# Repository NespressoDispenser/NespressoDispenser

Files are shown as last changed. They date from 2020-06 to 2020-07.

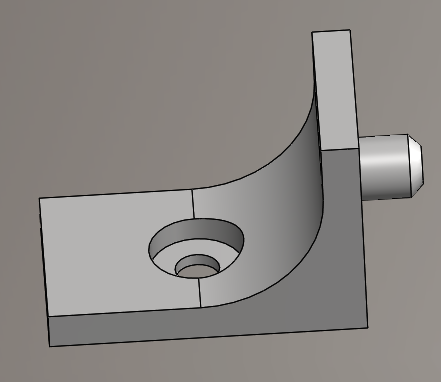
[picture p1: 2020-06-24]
3D prints/shelf bracket/shelf_bracket.png

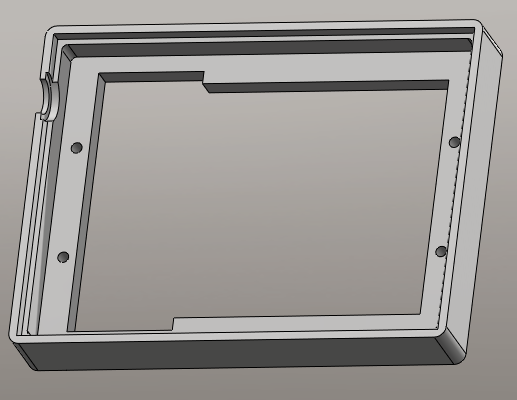
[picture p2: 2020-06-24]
3D prints/elatec reader mounting/reader_box_mounting.png

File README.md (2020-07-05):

# Nespresso dispenser machine
picture render
# Description
We are four students studying at the HEIG-VD in Switzerland and we've made this semester project. The purpose is to sell coffee capsule to anyone having a student card (Legic/Mifare) compatible with the Elatec reader.

- Affolter Luca: Modelling, system conception
- Fornerod Quentin: 3D printing, Github, RFID reader
- Fournier Loïc: Servomotors, LCD display
- Rosselli Jasmine: Touch sensors, Led strip

# Contact
If you have any question about the conception or any technichal interrogation, feel free to contact us:

Nespresso.Dispenser@gmail.com

# Youtube video
https://youtu.be/O0Zy7WqqgV4

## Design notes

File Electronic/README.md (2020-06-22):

# Description
The material we've used was mainly taken in the Fablab of the HEIG-VD

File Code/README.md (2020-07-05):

# Description
The Arduino codes are separated in two files:
- release version: contains the last code version uploaded on the machine

- test codes: contains primitives codes, some of them are not usefull but might be interesting

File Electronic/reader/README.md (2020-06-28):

# Description
Two softwares are available with the Elatec Reader:
- Director.exe
- AppBlaster.exe

# Director.exe
This programm is use to read any card via USB. In order to implement this, you have to load the right firmware USB

# AppBlaster.exe
This software allows you to custom the internal code of the Elatec reader. You have to create a source file (C programmed language) name it "App_HUS100_XXXXXXX_.c". You will then create a new firmware adding your source code file. Upload the firmware "TWN4_CCx322_HUS100_XXXXXXX.bix" in the device and you're ready to go. 

If something is unclear, please refer to the documentation "TWN4 API Reference DocRev24.pdf" and "TWN4 AppBlaster Config Cards User Guide DocRev10.pdf" and don't forget to check you wiring.

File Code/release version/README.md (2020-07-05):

# Description
We've used the *Arduino IDE* version 1.8.13 to compile and upload the code

The Arduino board is a ATMega 2560

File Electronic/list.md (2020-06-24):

# Description 
Complete list of material we bought for the project:
- 1x Elatec reader	T4DT-BB2BEL	
- 4x Inductive sensor	Lj6A3-2-z/BX	
- 2x Servo motors	SG92R	
- 2x Push button	(Any N-O button)	
- 2x40cm (2x26 leds) Led strip WS2812	
- 1x LCD screen 16x2	NHD-0216K1Z-NSW-FBW-L-ND 	
- 1x Arduino Mega	Clone	
- 1x SD module	Micro SD TF Card Adapter	
- 1x Sd card	(Any)	
- 1x Power supply	12VDC XXXXW	
- 4x Touch sensor	SH150917

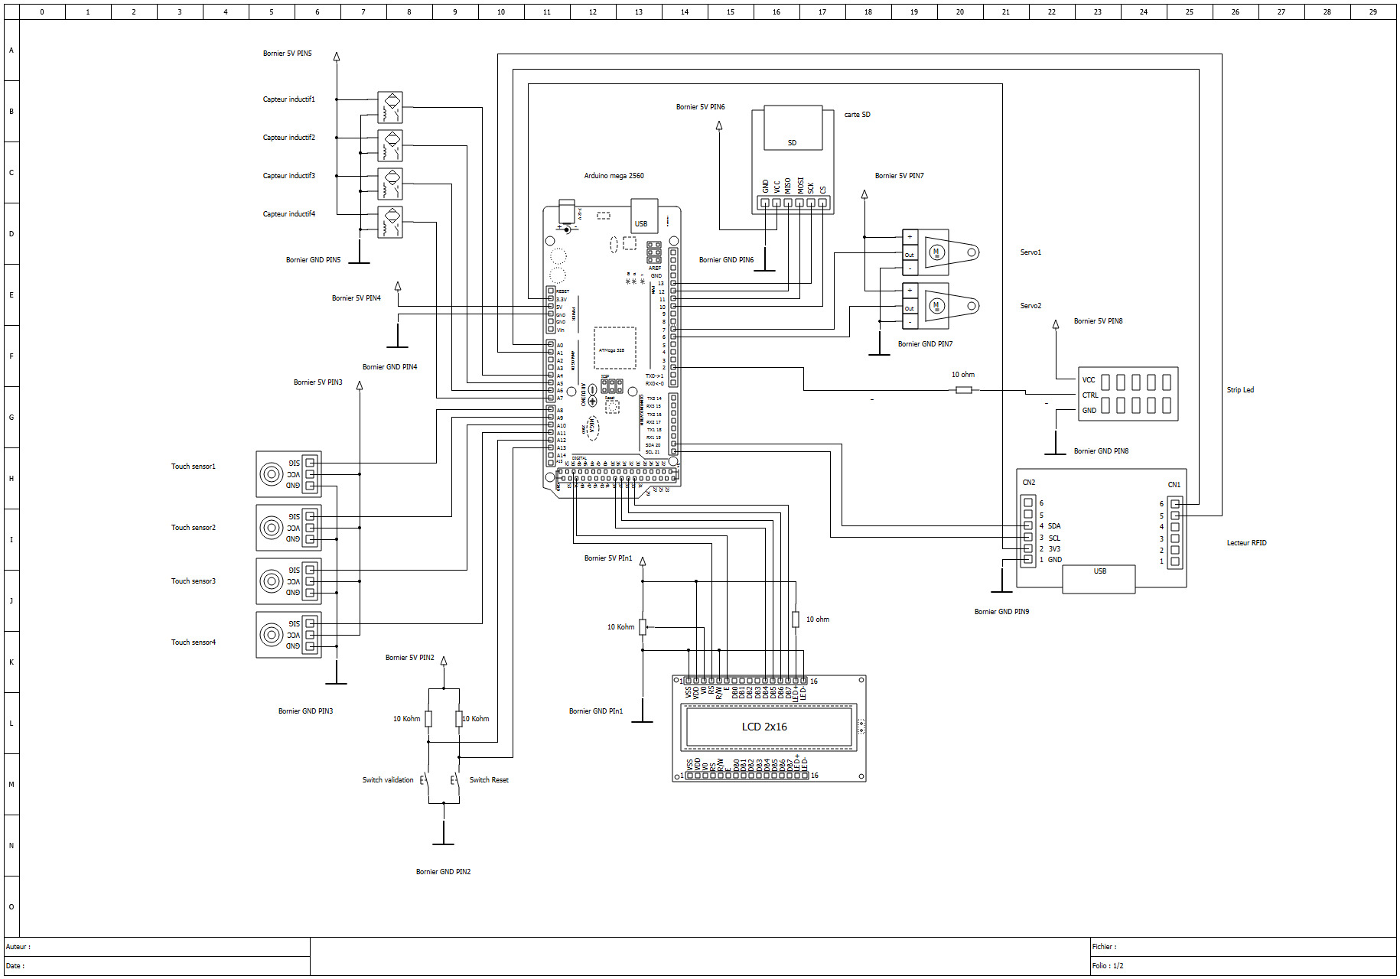
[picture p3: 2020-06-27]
Electronic/electronic_schematic.jpeg

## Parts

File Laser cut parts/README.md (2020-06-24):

# Description
The machine used for all the cuts (PPMA, MDF) is the Trotec Speedy 360. The thickness and the material of every part is mentionned in the file. Comments and filenames are in french.

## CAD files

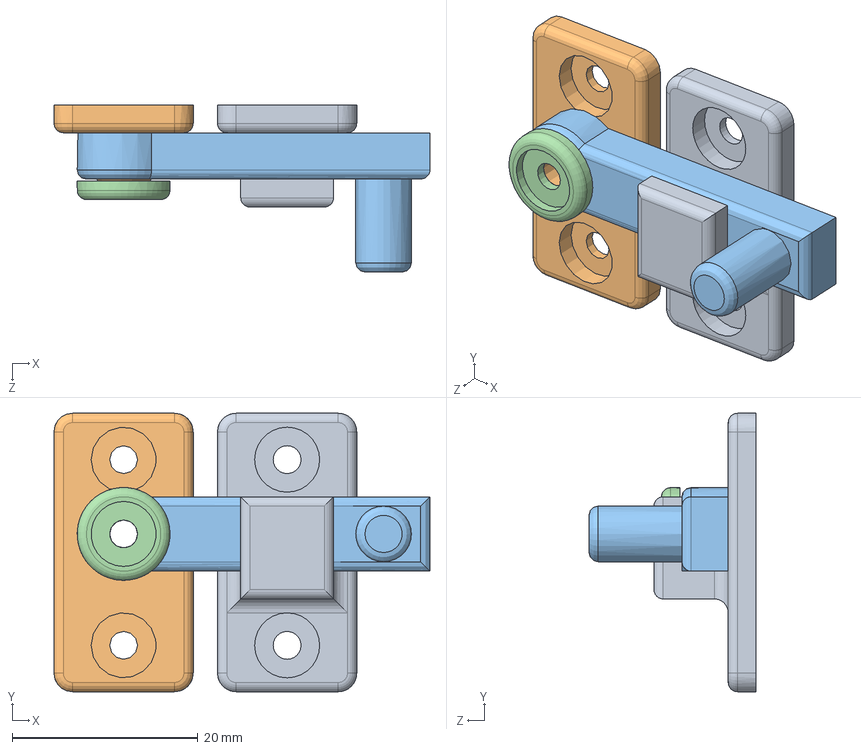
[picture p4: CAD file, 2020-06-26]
3D prints/door lock/asmb_door_lock.SLDASM
40.5 x 30.0 x 18.0 mm
door_lock_part1
door_lock_part2
door_lock_part3
door_lock_part4

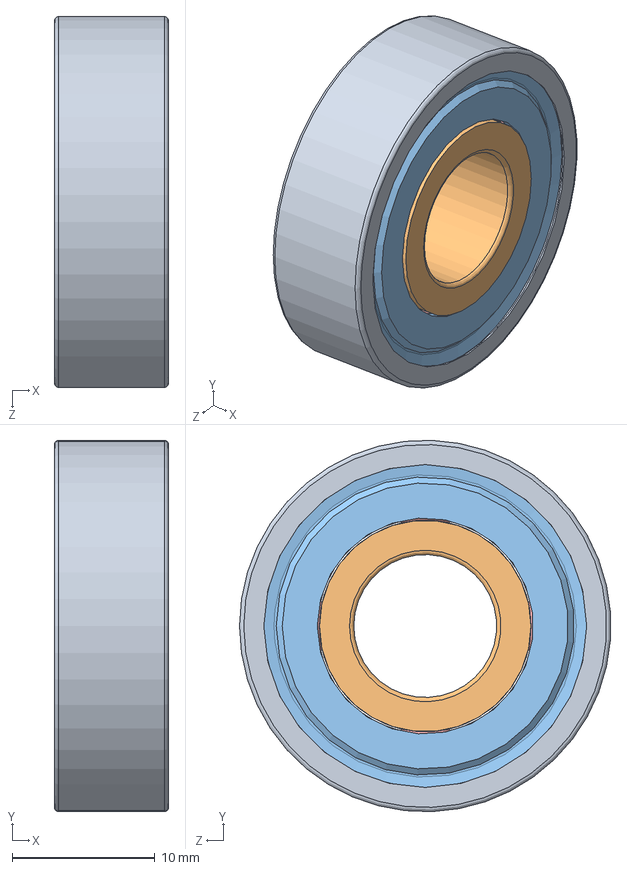
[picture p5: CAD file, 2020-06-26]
Assembly/roulement_6000-2z_1.SLDASM
8.00 x 26.0 x 26.0 mm
roulement_6000-2z_1_01
roulement_6000-2z_1_02
roulement_6000-2z_1_03
roulement_6000-2z_1_04
roulement_6000-2z_1_05

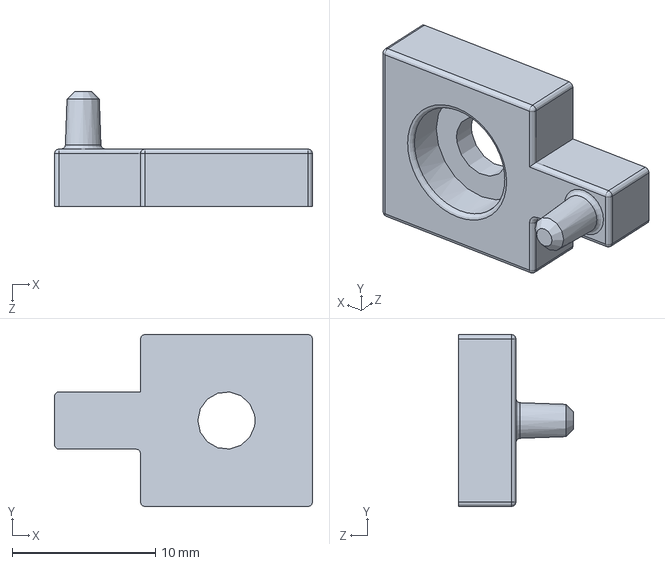
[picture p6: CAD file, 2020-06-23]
3D prints/arduino mega mounting/arduino_mega_mounting.SLDPRT
18.0 x 12.0 x 8.00 mm

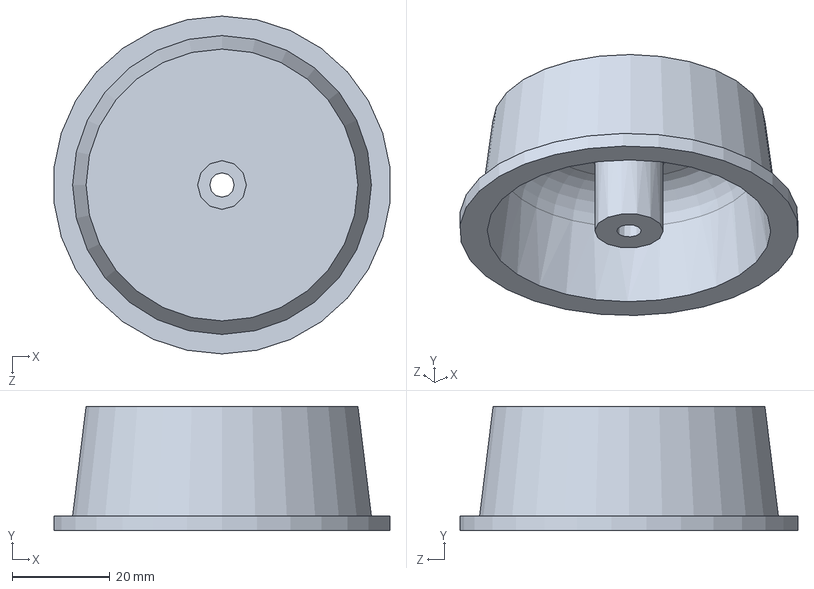
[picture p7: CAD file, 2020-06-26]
3D prints/cup holder/cup_holder_small_empty.SLDPRT
68.9 x 25.5 x 69.3 mm

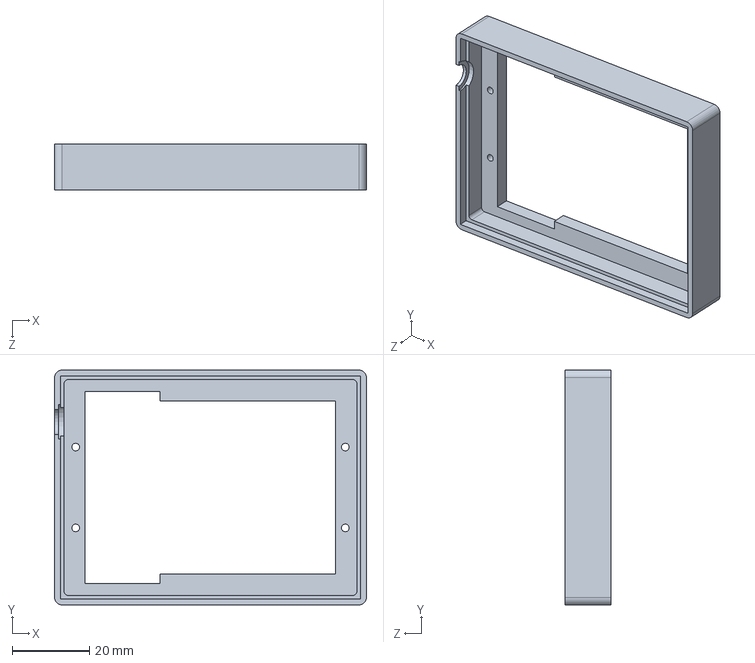
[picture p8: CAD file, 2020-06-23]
3D prints/elatec reader mounting/reader_box_mounting.SLDPRT
81.0 x 61.0 x 12.0 mm

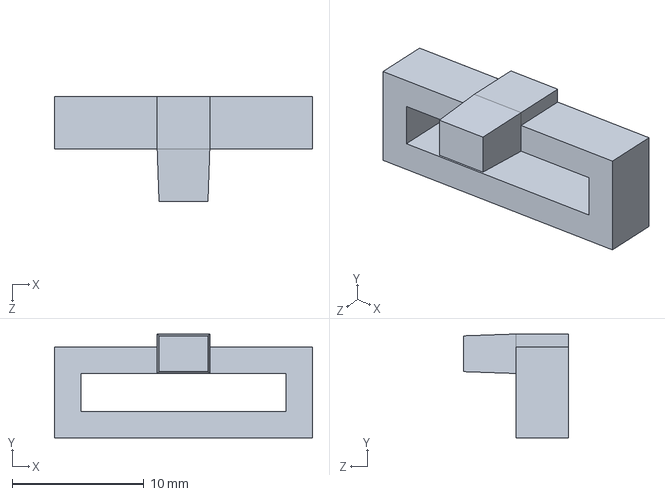
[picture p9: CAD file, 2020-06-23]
3D prints/encoding lug reader/encoding_lug_reader.SLDPRT
19.6 x 7.90 x 8.00 mm

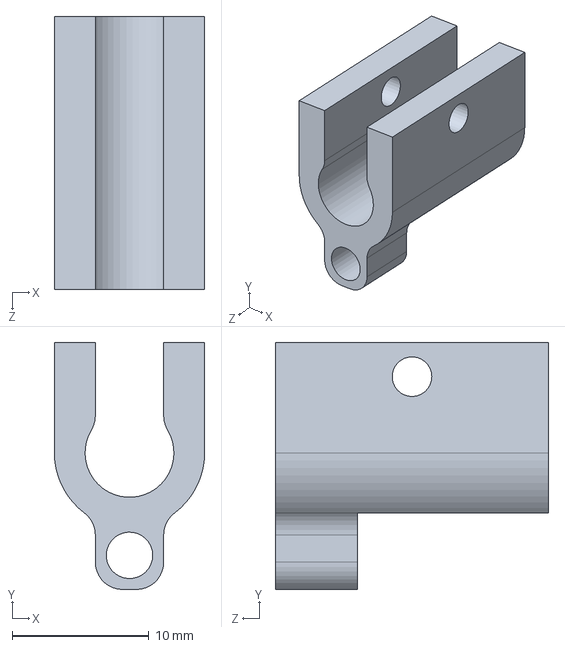
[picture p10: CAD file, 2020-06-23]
3D prints/inductive sensor mounting/inductive_sensor.SLDPRT
11.0 x 18.1 x 20.0 mm

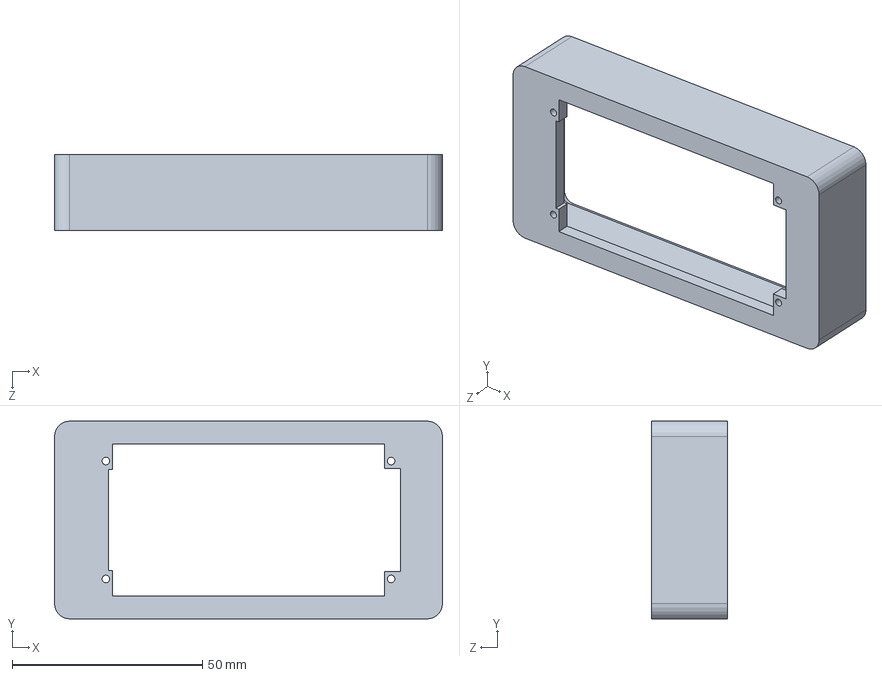
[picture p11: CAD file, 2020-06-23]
3D prints/LCD mounting/LCD_box_mounting.SLDPRT
102.0 x 52.0 x 20.0 mm

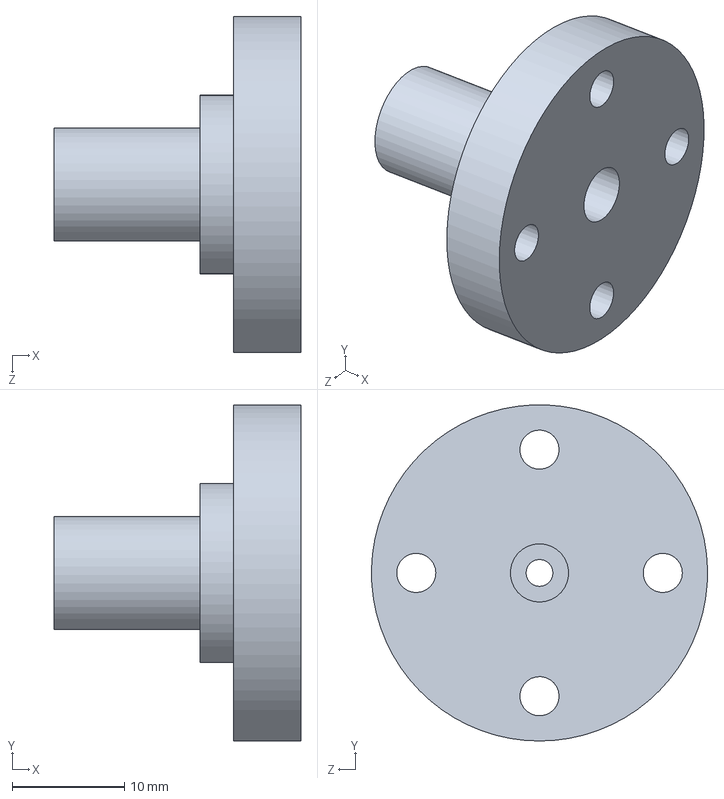
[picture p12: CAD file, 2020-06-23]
3D prints/motor coupling SG92/motor_coupling_sg92.SLDPRT
22.0 x 30.0 x 30.0 mm

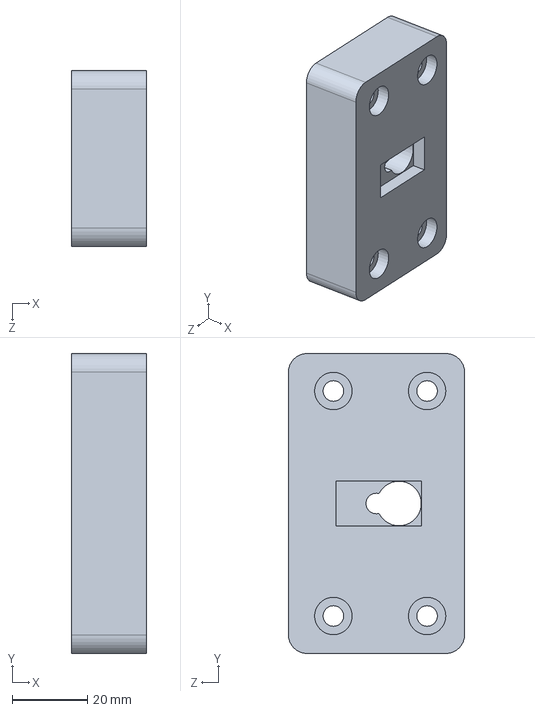
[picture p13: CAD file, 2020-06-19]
3D prints/motor mounting/motor_coupling.SLDPRT
20.0 x 80.0 x 47.0 mm

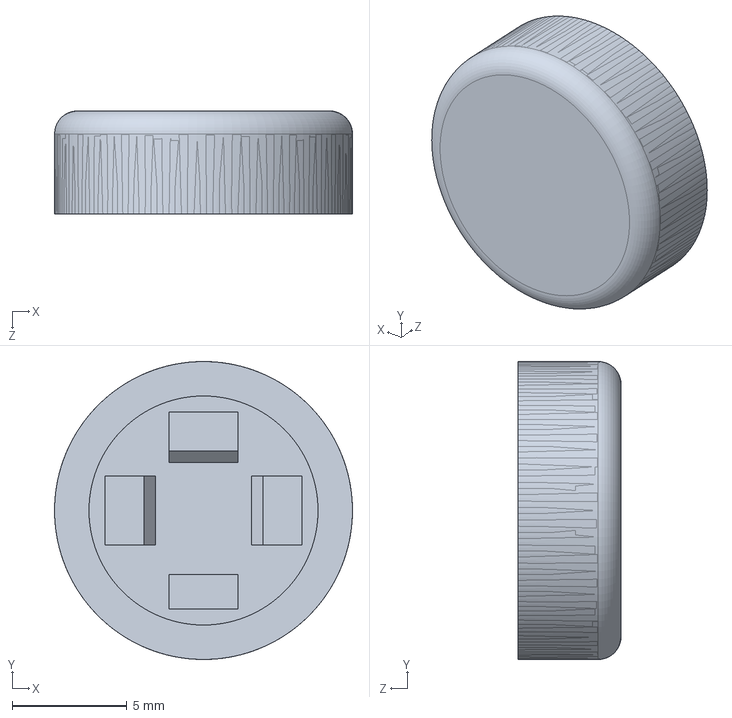
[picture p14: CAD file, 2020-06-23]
3D prints/push button cover/push_button_cover.SLDPRT
13.0 x 13.0 x 4.50 mm

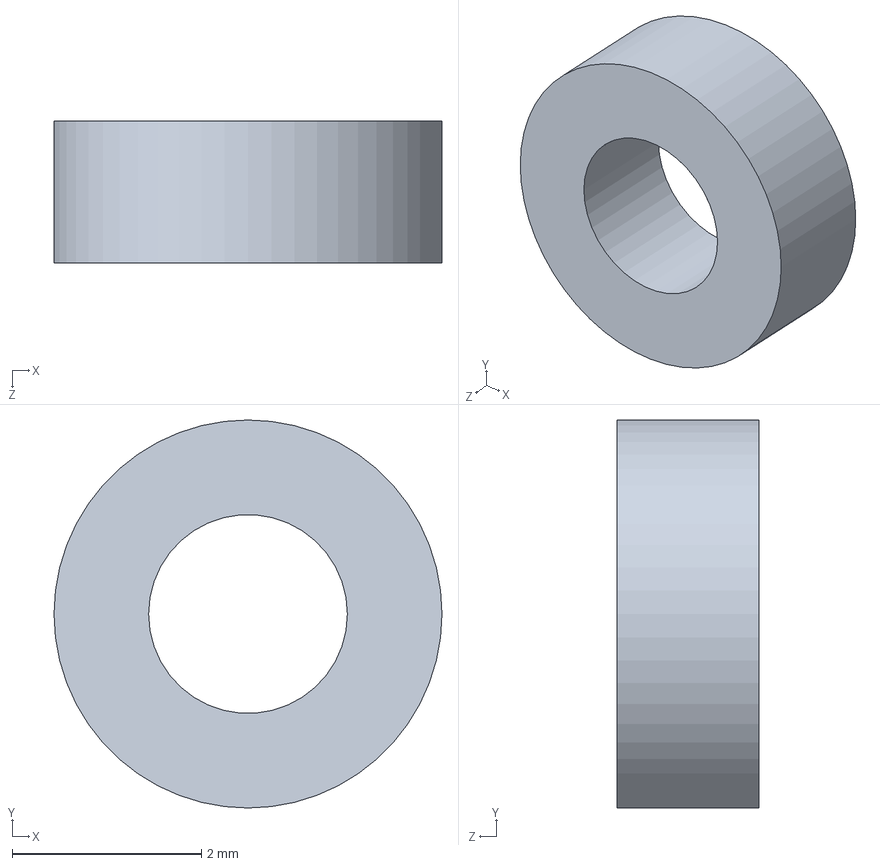
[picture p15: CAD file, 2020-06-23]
3D prints/SD module spacer/SD_module_spacer.SLDPRT
4.10 x 4.10 x 1.50 mm

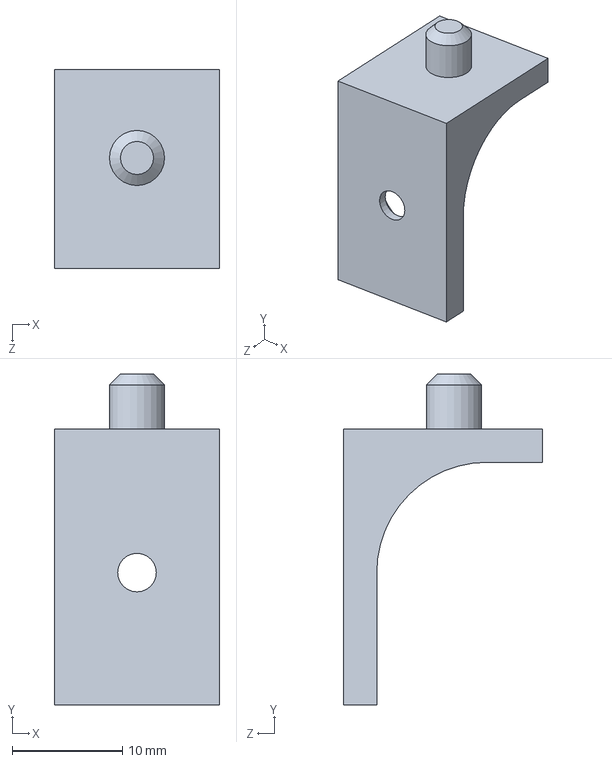
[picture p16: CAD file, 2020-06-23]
3D prints/shelf bracket/shelf bracket.SLDPRT
15.0 x 30.0 x 18.0 mm

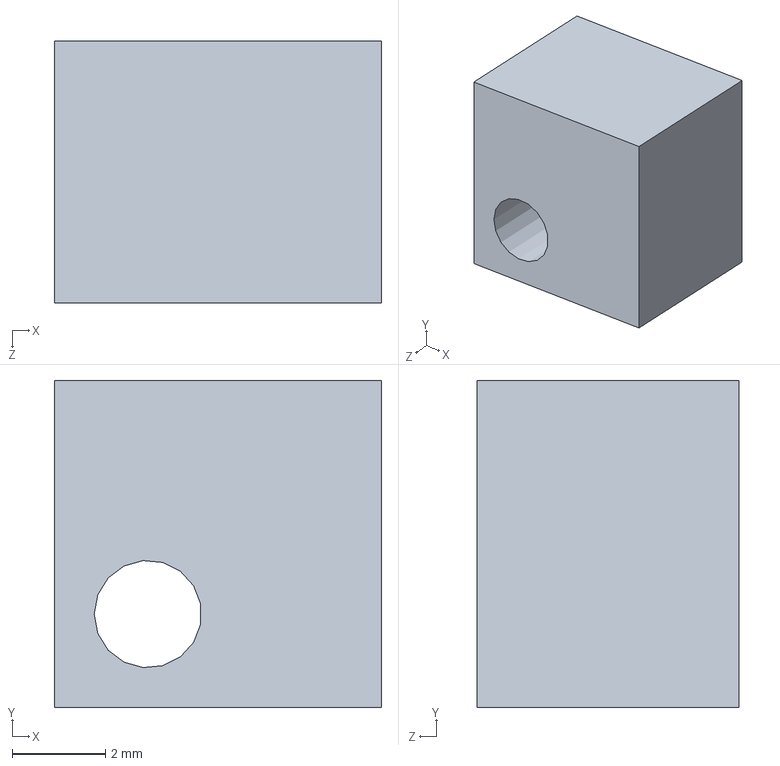
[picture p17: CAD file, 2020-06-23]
3D prints/touch sensor mounting/touch_sensor_mounting.SLDPRT
7.00 x 7.00 x 5.60 mm

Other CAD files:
Laser cut parts/plexiglass board (PMMA)/03_00 front pannel/03_00_Plexi_face.DXF
Laser cut parts/plexiglass board (PMMA)/03_01 merchandiser capsule pannel/03_01_Plexi_prsentoire.DXF
Laser cut parts/plexiglass board (PMMA)/03_02 led strip cover/03_02_Plexiglas_prsentoire_capsule.DXF
Laser cut parts/wooden board (MDF)/00_00 back pannel/00_00_Panneau_arriere.DXF
3D prints/LCD mounting/LCD_box_cover.SLDPRT
3D prints/LCD mounting/LCD_box_cover.STL
3D prints/LCD mounting/LCD_box_mounting.STL
3D prints/SD module spacer/SD_module_spacer.STL
3D prints/arduino mega mounting/arduino_mega_mounting.STL
3D prints/cup holder/cup_holder_big_empty.SLDPRT
3D prints/cup holder/cup_holder_big_empty.STL
3D prints/cup holder/cup_holder_small_empty.STL
3D prints/door lock/door_lock_part1.SLDPRT
3D prints/door lock/door_lock_part1.STL
3D prints/door lock/door_lock_part2.SLDPRT
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

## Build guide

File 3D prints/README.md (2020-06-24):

# Description
This folder contain all the files of the 3D printed parts. Each folder contains 3 files: 
- Stereolithographics files (.STL) 
- Modelised part (.SLDPRT)
- Picture (.png/.JPEG)

# Printing
The slicer software used is *Cura V4.6*, printing parameters will change upon the printing machine and won't be mentionned.
All impressions are made of PLA

# Modelling
All parts have been modelised with *Solidworks 2018 SP5.0* 

# Render
A picture of each modelised parts 

# Complementary informations
The file *list.md* specifies the number of each printed part used for the construction

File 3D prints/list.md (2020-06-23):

# Description
The list mentions the number of each piece printed for the project. The number of 3D prints may be different depending on your design choice.
# 3D parts
- 1x LCD mounting
- 4x SD module spacer
- 4x arduino mega mounting
- 1x door lock (each part)
- 1x elactec reader mounting (each part)
- 2x encoding lug reader
- 4x inductive sensor mounting
- 2x motor coupling SG92
- 2x motor mounting
- 2x push button cover (different colors)
- 4x shelf bracket
- 8x touch sensor mounting

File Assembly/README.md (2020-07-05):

# Render
modelling_machine

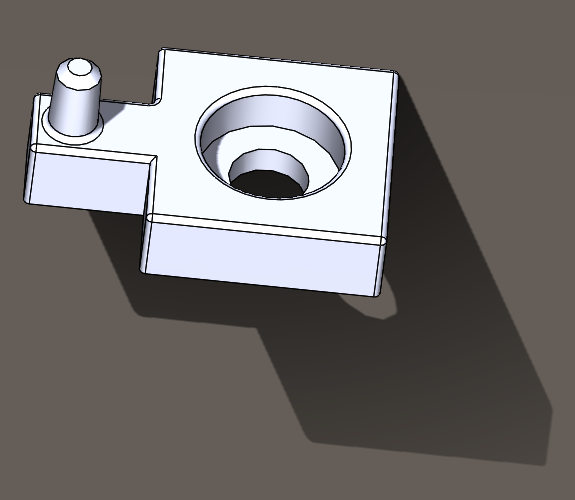
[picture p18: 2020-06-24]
3D prints/arduino mega mounting/arduino_mounting.png

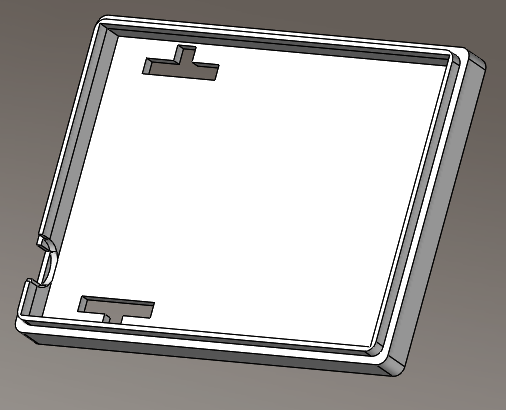
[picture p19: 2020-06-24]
3D prints/elatec reader mounting/reader_box_cover.png

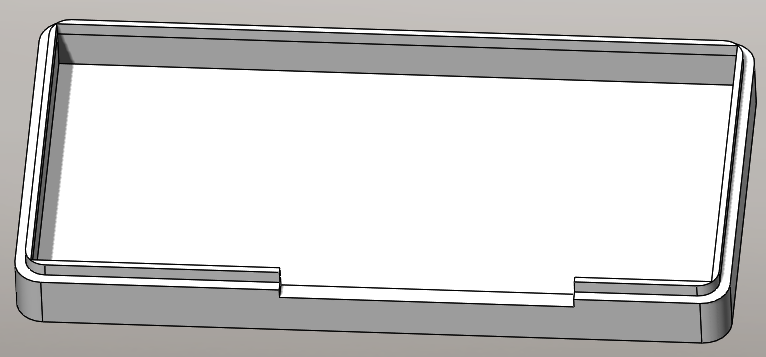
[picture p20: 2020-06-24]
3D prints/LCD mounting/LCD_box_cover.png

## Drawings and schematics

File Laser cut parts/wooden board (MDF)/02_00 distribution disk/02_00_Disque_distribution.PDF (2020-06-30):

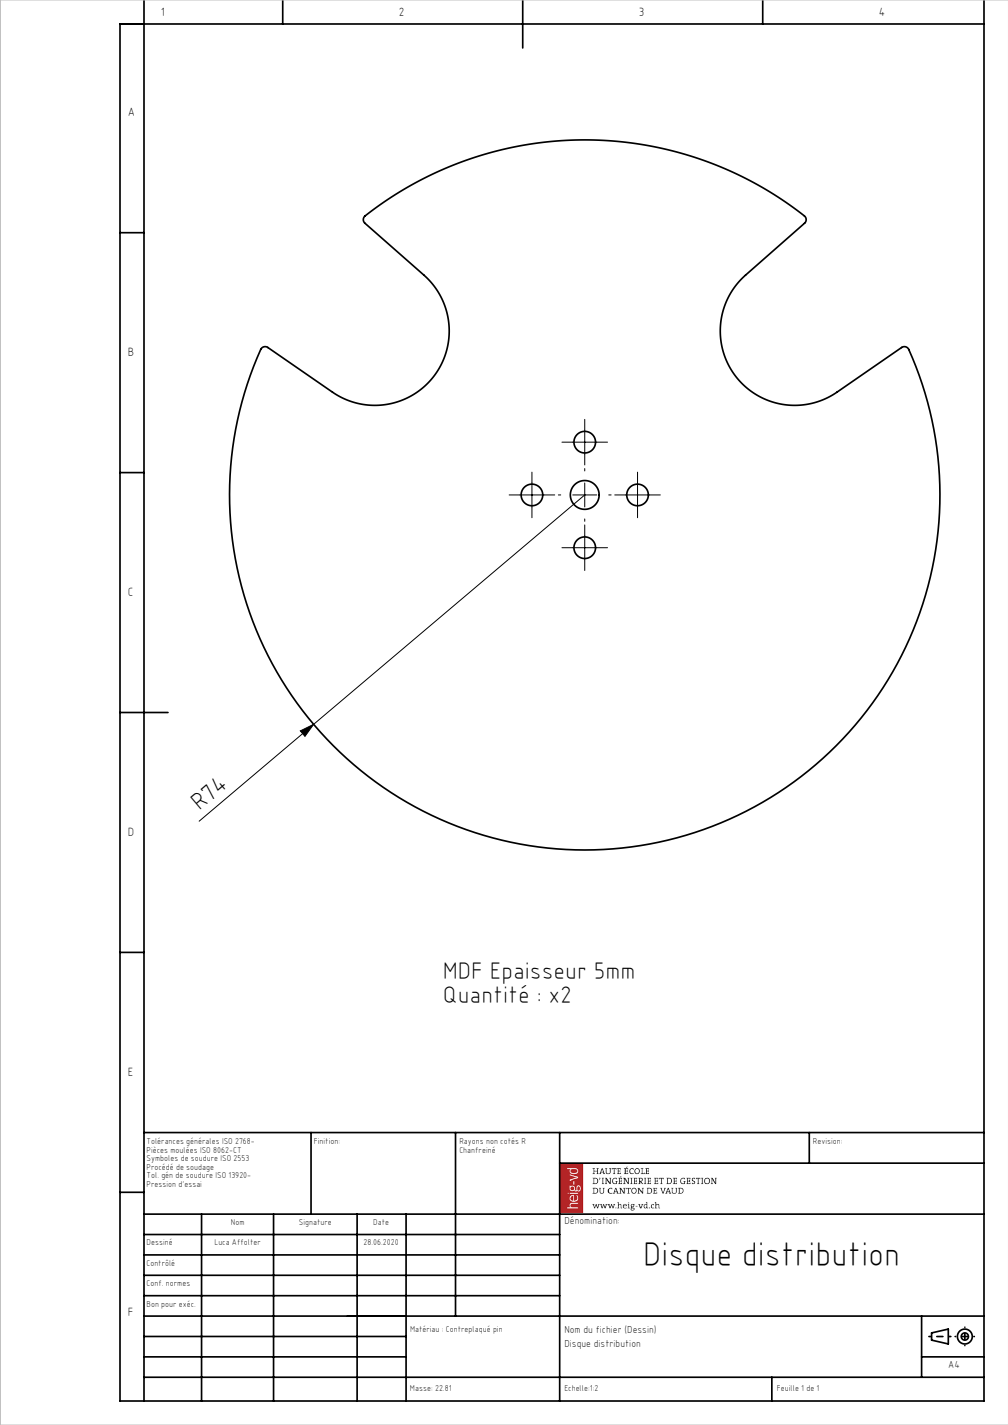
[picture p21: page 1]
MDF Epaisseur 5mm Quantité : x2; Masse: 22.81; Conf. normes; Bon pour exéc.; Feuille 1 de 1; Luca Affolter; Disque distribution

Tolérances générales ISO 2768-
Pièces moulées ISO 8062-CT
Symboles de soudure ISO 2553
Procédé de soudage
Tol. gén de soudure ISO 13920-
Pression d'essai

Rayons non cotés R
Chanfreiné

Matériau : Contreplaqué pin

Nom du fichier (Dessin)
Disque distribution

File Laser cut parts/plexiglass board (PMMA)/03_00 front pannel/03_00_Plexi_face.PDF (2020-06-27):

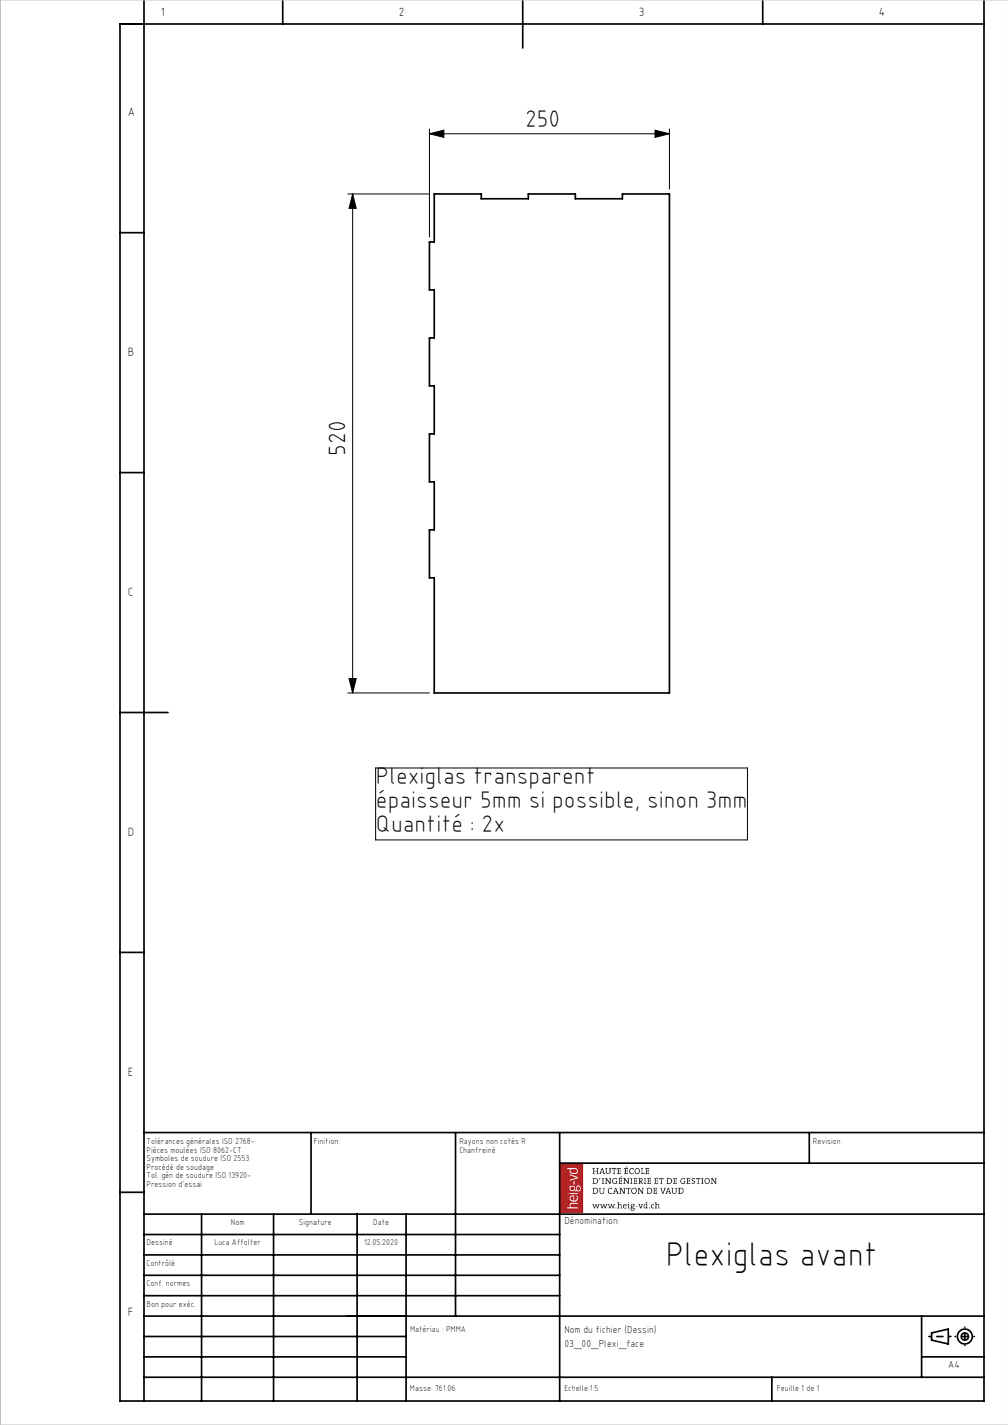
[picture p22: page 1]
Matériau : PMMA; Masse: 761.06; Conf. normes; Bon pour exéc.; Feuille 1 de 1; Luca Affolter; Plexiglas avant

Plexiglas transparent
épaisseur 5mm si possible, sinon 3mm
Quantité : 2x

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

Rayons non cotés R
Chanfreiné

Nom du fichier (Dessin)
03_00_Plexi_face

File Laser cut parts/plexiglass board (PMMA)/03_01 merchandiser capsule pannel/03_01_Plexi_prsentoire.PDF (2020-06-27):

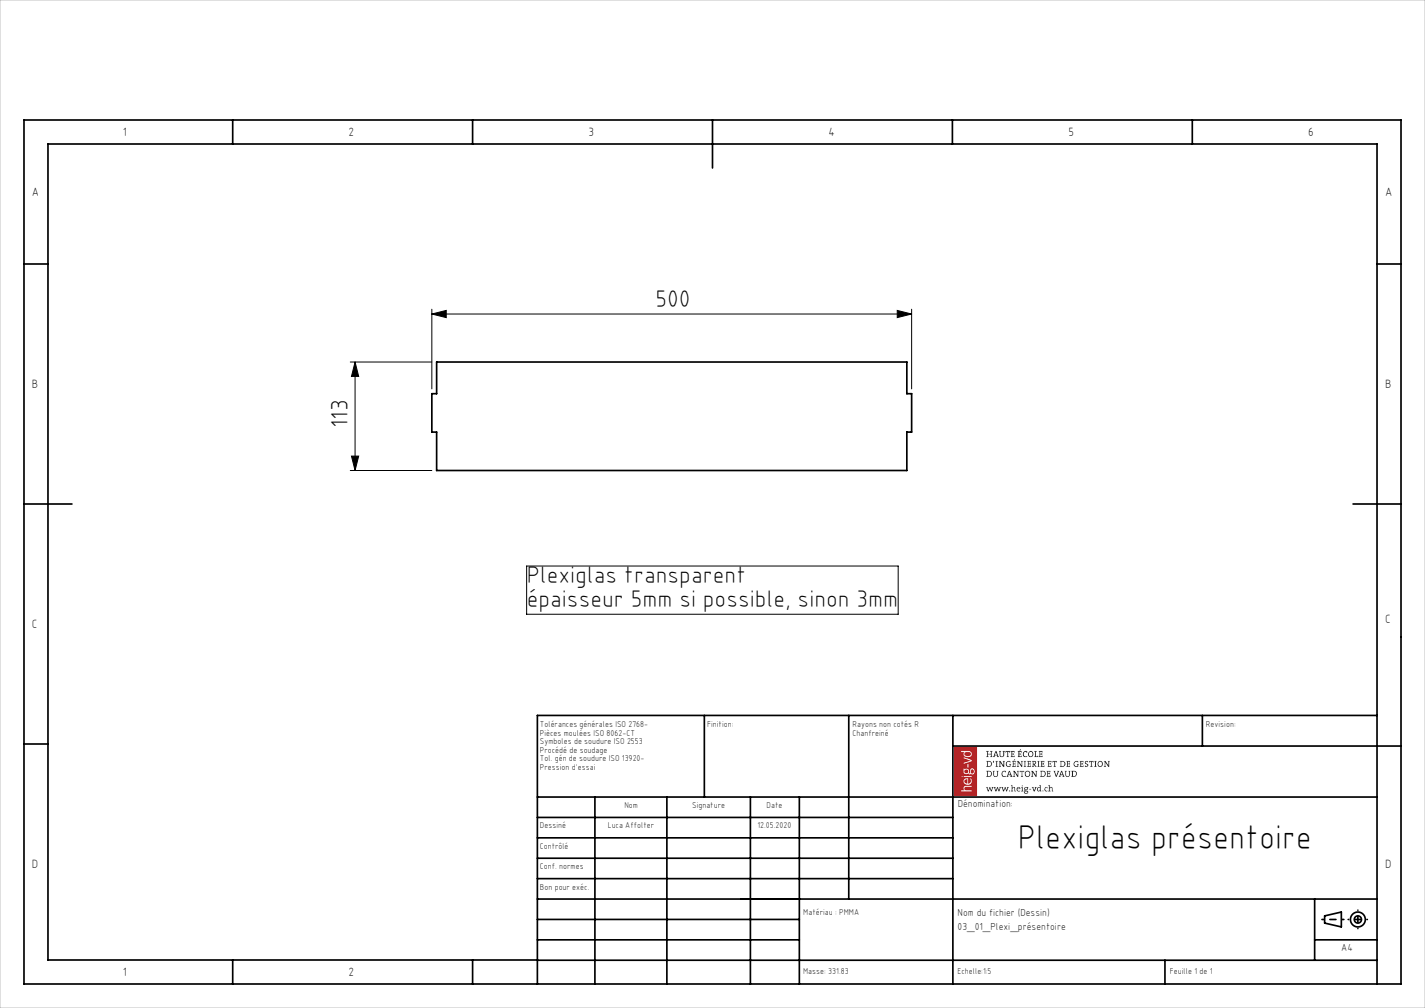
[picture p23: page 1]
Plexiglas présentoire; Luca Affolter; Feuille 1 de 1; Finition:; Rayons non cotés R; Masse: 331.83; Matériau : PMMA

Plexiglas transparent
épaisseur 5mm si possible, sinon 3mm

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

Dessiné
Contrôlé
Conf. normes
Bon pour exéc.

Nom du fichier (Dessin)
03_01_Plexi_présentoire

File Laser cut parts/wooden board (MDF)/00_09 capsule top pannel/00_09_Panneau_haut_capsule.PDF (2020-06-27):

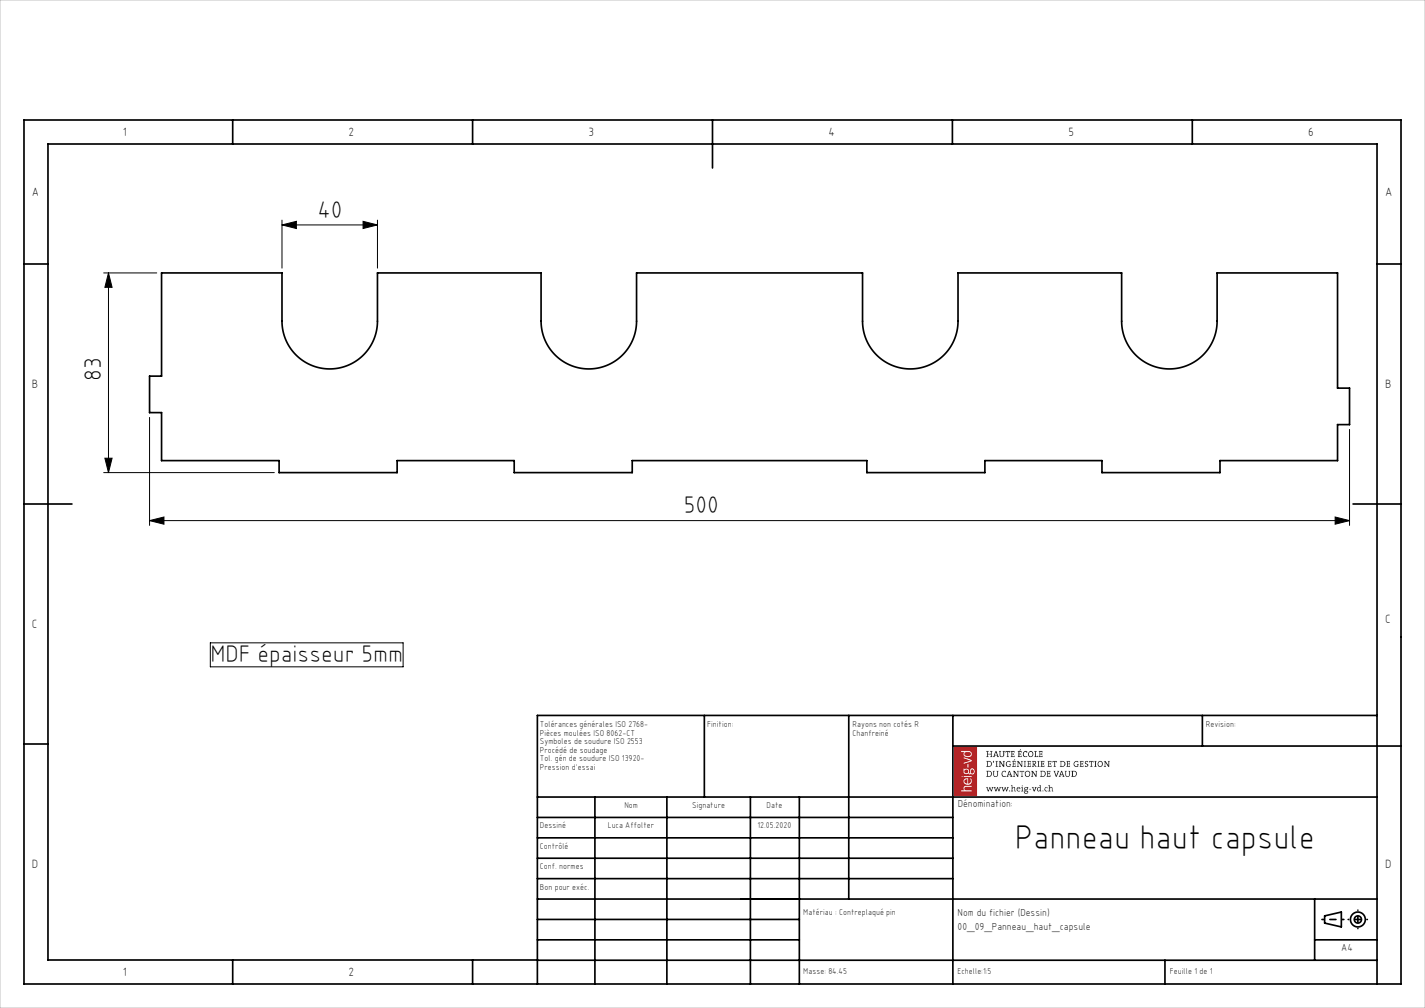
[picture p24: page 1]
MDF épaisseur 5mm; Luca Affolter; Feuille 1 de 1; Finition:; Rayons non cotés R; Masse: 84.45

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

Dénomination:
Panneau haut capsule

Dessiné
Contrôlé
Conf. normes
Bon pour exéc.

Matériau : Contreplaqué pin

Nom du fichier (Dessin)
00_09_Panneau_haut_capsule

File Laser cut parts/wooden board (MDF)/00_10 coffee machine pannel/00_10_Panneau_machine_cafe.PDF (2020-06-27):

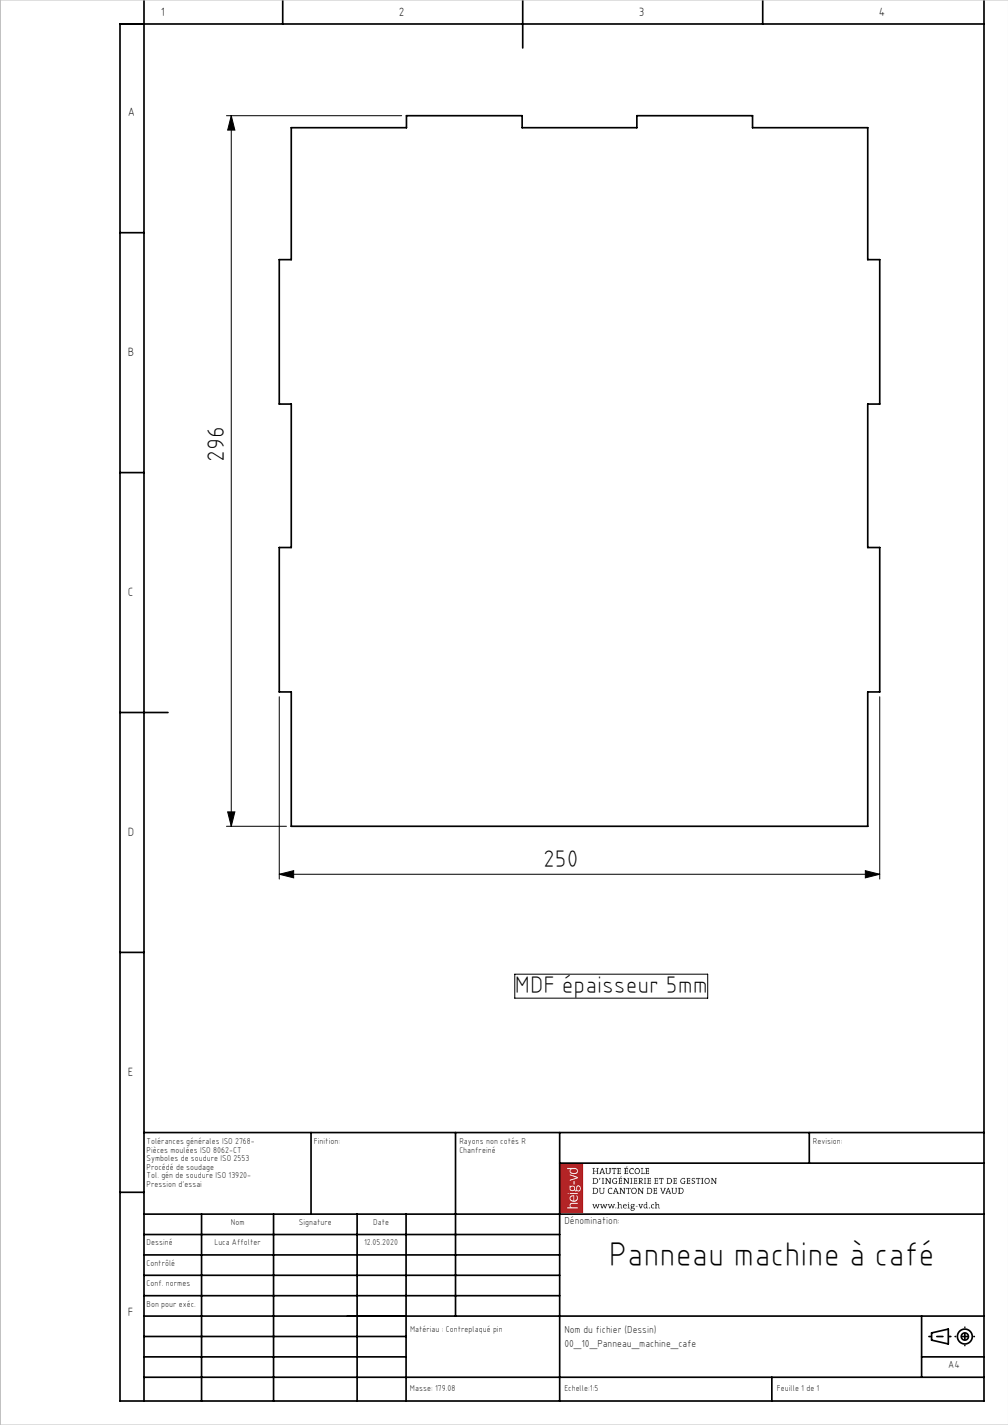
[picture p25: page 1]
MDF épaisseur 5mm; Masse: 179.08; Conf. normes; Bon pour exéc.; Feuille 1 de 1; Luca Affolter

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

Rayons non cotés R
Chanfreiné

Dénomination:
Panneau machine à café

Matériau : Contreplaqué pin

Nom du fichier (Dessin)
00_10_Panneau_machine_cafe

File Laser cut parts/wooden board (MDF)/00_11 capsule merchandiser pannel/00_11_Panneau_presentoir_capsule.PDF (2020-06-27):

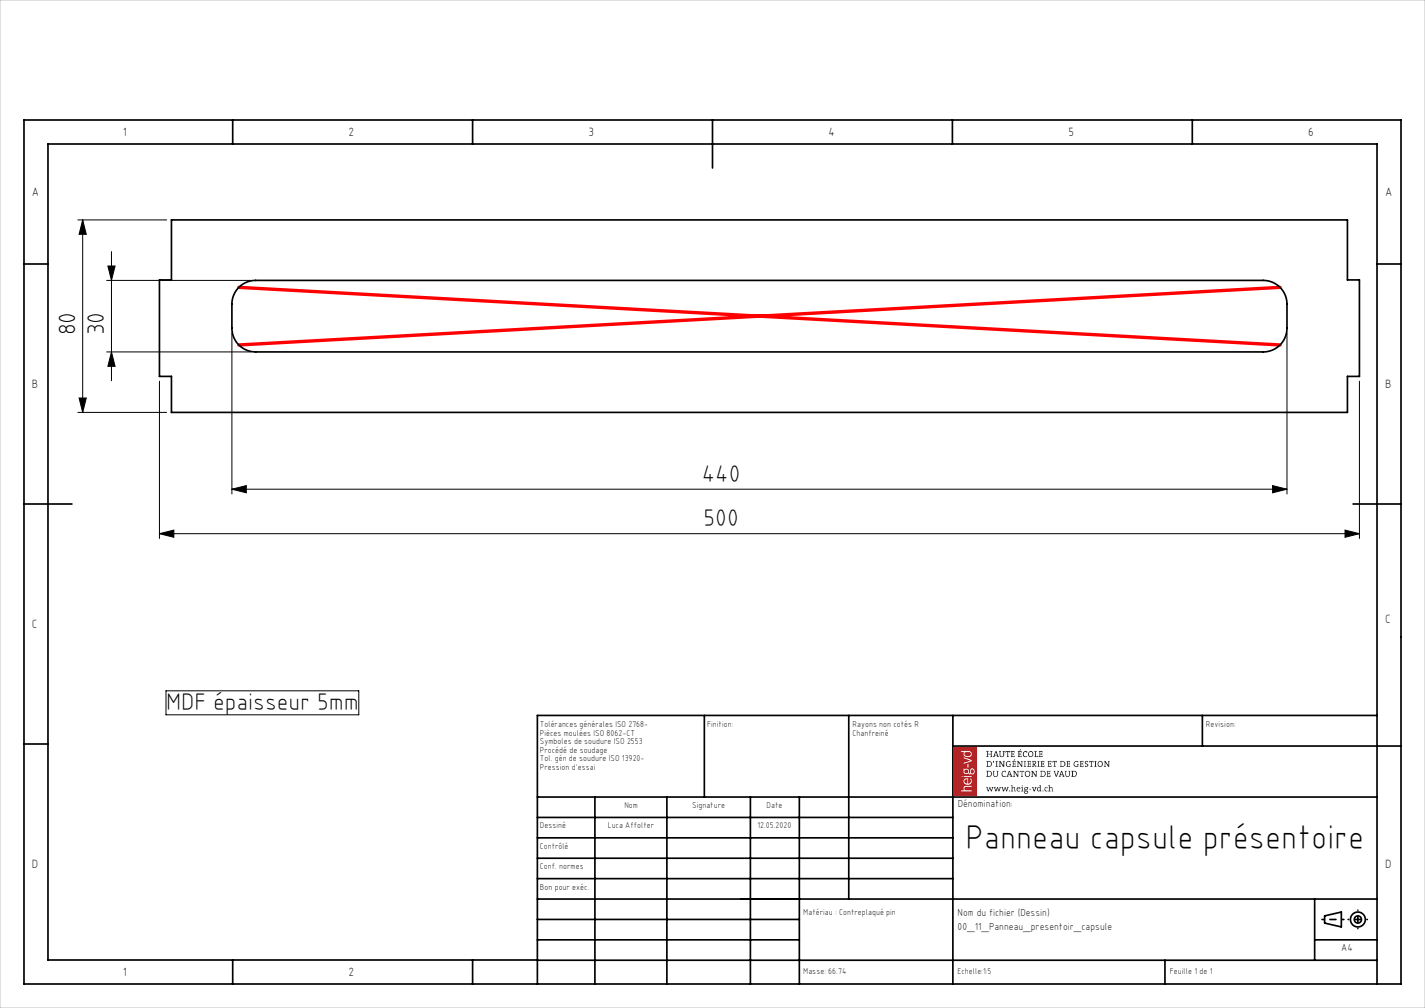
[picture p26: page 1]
MDF épaisseur 5mm; Luca Affolter; Feuille 1 de 1; Finition:; Rayons non cotés R; Masse: 66.74

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

Dénomination:
Panneau capsule présentoire

Dessiné
Contrôlé
Conf. normes
Bon pour exéc.

Matériau : Contreplaqué pin

Nom du fichier (Dessin)
00_11_Panneau_presentoir_capsule

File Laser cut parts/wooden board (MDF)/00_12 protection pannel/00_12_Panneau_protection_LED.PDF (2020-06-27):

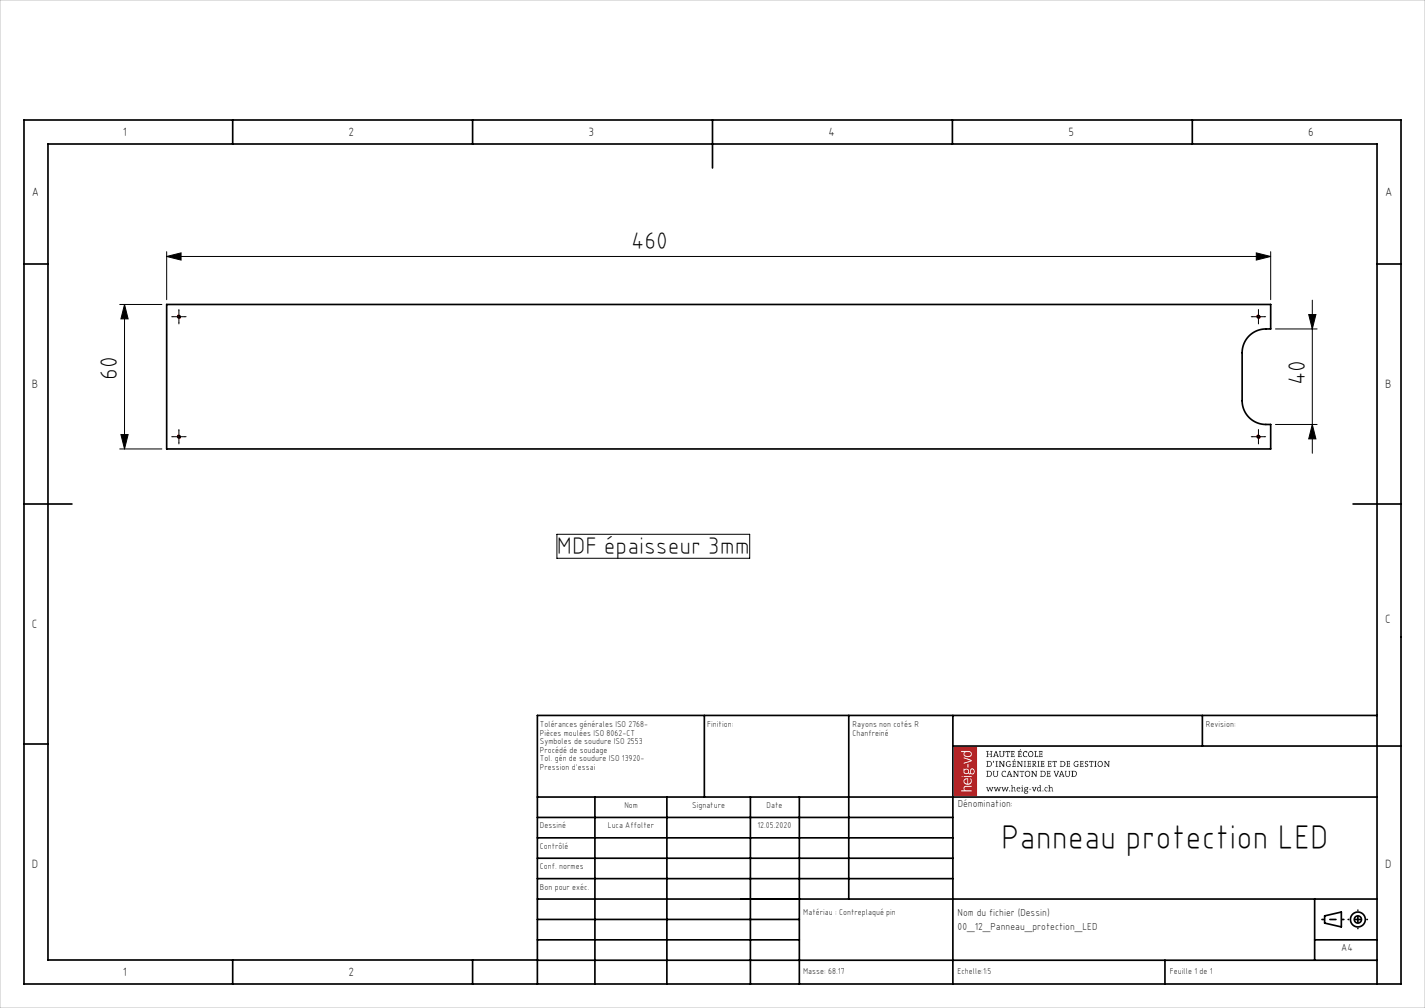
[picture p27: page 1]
MDF épaisseur 3mm; Luca Affolter; Feuille 1 de 1; Finition:; Rayons non cotés R; Masse: 68.17

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

Dénomination:
Panneau protection LED

Dessiné
Contrôlé
Conf. normes
Bon pour exéc.

Matériau : Contreplaqué pin

Nom du fichier (Dessin)
00_12_Panneau_protection_LED

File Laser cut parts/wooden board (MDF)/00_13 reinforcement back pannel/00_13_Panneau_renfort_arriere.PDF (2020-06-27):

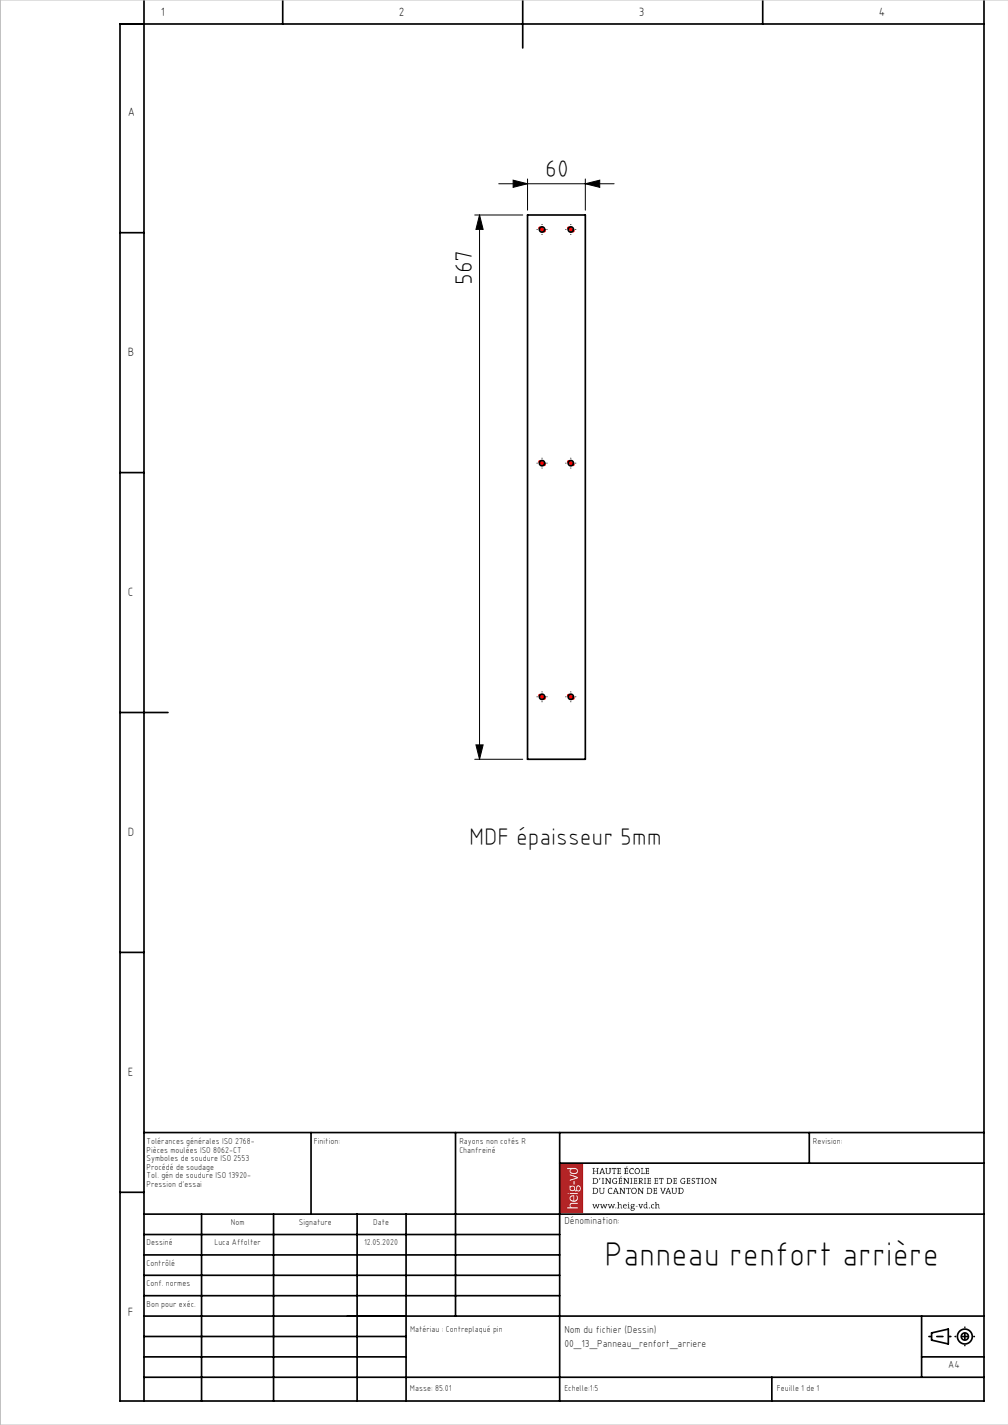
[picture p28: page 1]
MDF épaisseur 5mm; Masse: 85.01; Conf. normes; Bon pour exéc.; Feuille 1 de 1; Luca Affolter

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

Rayons non cotés R
Chanfreiné

Dénomination:
Panneau renfort arrière

Matériau : Contreplaqué pin

Nom du fichier (Dessin)
00_13_Panneau_renfort_arriere

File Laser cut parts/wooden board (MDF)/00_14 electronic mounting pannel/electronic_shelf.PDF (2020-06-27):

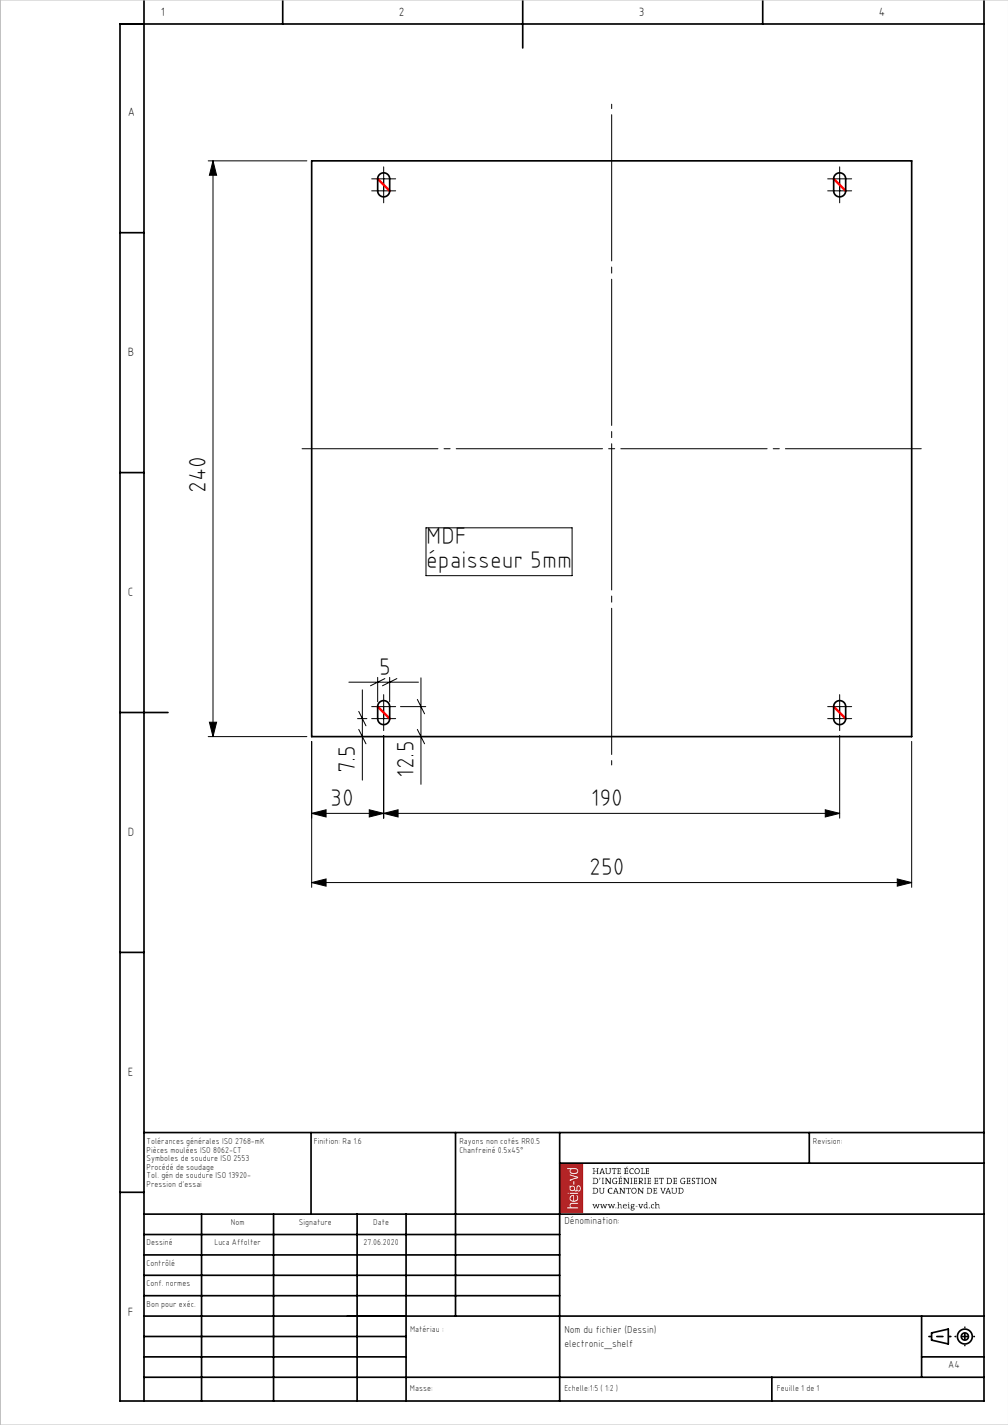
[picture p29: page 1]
épaisseur 5mm; Matériau :; Conf. normes; Bon pour exéc.; Finition: Ra 1.6; Feuille 1 de 1; Luca Affolter; Echelle:1:5 ( 1:2 )

Tolérances générales ISO 2768-mK
Pièces moulées ISO 8062-CT
Symboles de soudure ISO 2553
Procédé de soudage
Tol. gén de soudure ISO 13920-
Pression d'essai

Rayons non cotés RR0.5
Chanfreiné 0.5x45°

Nom du fichier (Dessin)
electronic_shelf

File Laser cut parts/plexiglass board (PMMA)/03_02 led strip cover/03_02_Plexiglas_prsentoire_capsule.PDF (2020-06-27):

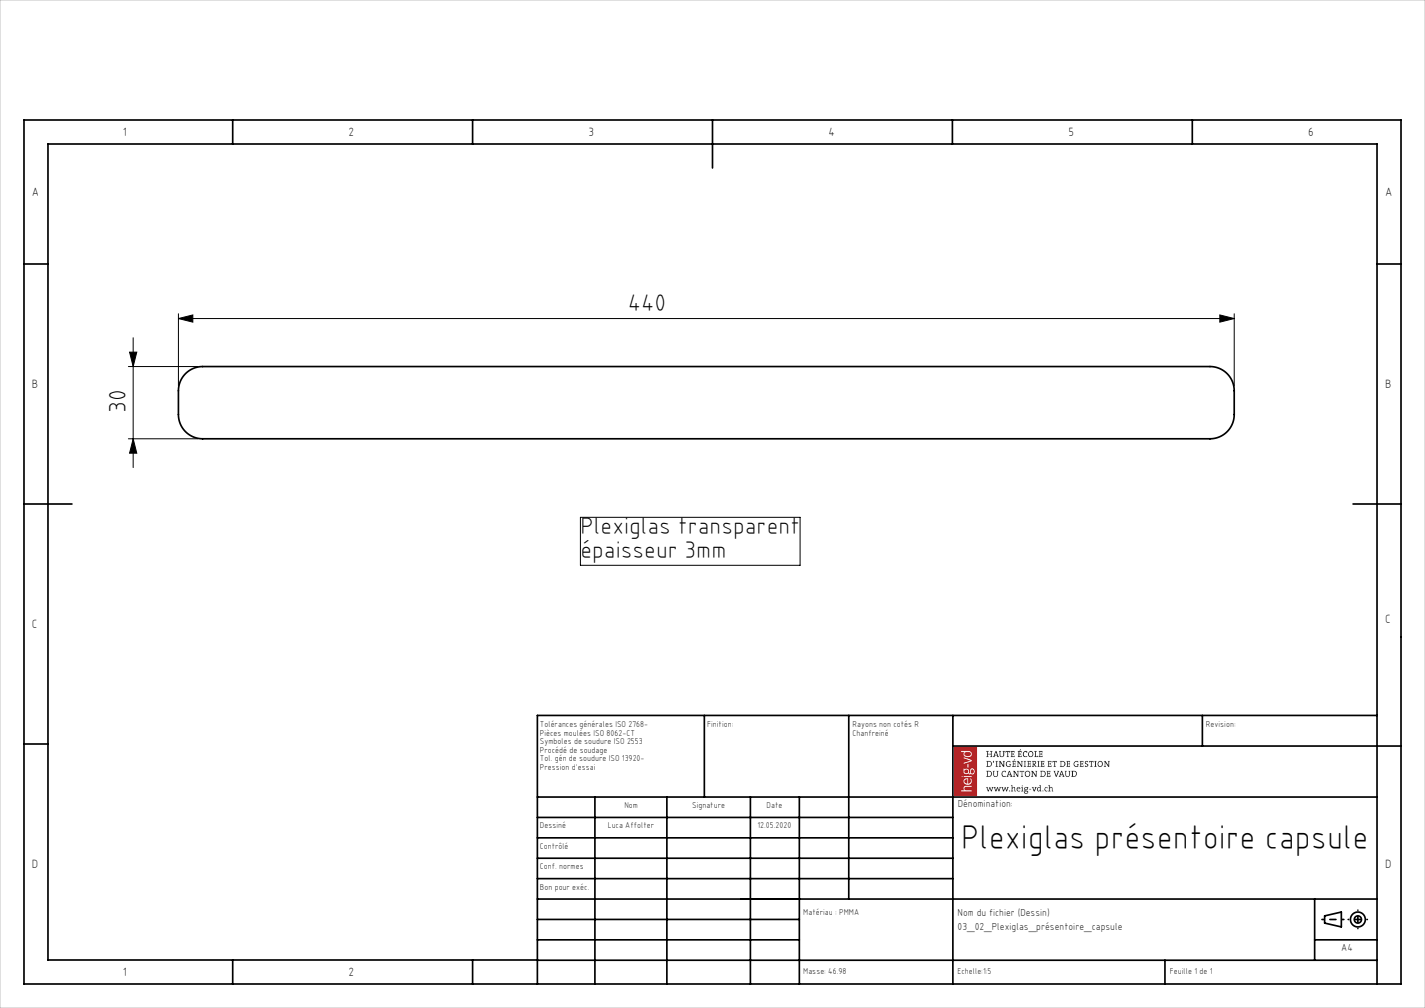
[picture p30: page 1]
Plexiglas transparent épaisseur 3mm; Luca Affolter; Feuille 1 de 1; Finition:; Rayons non cotés R; Masse: 46.98; Matériau : PMMA

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

Dénomination:
Plexiglas présentoire capsule

Dessiné
Contrôlé
Conf. normes
Bon pour exéc.

Nom du fichier (Dessin)
03_02_Plexiglas_présentoire_capsule

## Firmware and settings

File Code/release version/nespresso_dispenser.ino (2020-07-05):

//--|Include user|---------------------------------------------------------------------------
#include "nespresso_dispenser.h"
//-------------------------------------------------------------------------------------------
//----|Setup|--------------------------------------------------------------------------------
//detection capsule
bool sensor_capsule;
bool sensor_capsule_1;
bool sensor_capsule_2;
bool sensor_capsule_3;
bool sensor_capsule_4;
int num_sensor;
/*----------------Leds----------------------*/
CRGB strip_leds[NUM_LEDS];
const unsigned int capsule_1 = 3;
const unsigned int capsule_2 = 2;
const unsigned int capsule_3 = 1;
const unsigned int capsule_4 = 0;
/*----------------Switch-----------------------*/
//touch sensor 1-4
bool choice_1_active = false;
bool choice_2_active = false;
bool choice_3_active = false;
bool choice_4_active = false;
//confirm push button
bool confirm_active = false;
//cancel push button
bool cancel_active = false;
/*----------------Servomoteur-----------------------*/
//servo 1
sServo servo_1;
Servo order_servo_1;
//servo 2
sServo servo_2;
Servo order_servo_2;
//Fin de course
uint16_t end_position;
/*----------------LCD-----------------------*/
Adafruit_LiquidCrystal LCD(LCD_PINS);

/*----------------State Machine-----------------------*/
eState state_machine;
/*---------------old_time-----------------------*/
uint32_t old_time;
uint8_t capteurCapsuleDispo;
bool rfid;
int argentSuffisant;

USER active_user;
USER user1;
USER user2;

void receiveEvent(int howMany)
{
  int i = 0;
  while (Wire.available()) // loop through all
  {
    byte c = Wire.read();
    active_user.set_id(c, i);
    i++;
  }
  //we've decided to compare only the third byte for the demo
  if (active_user.get_id(3) == user1.get_id(3)) {
    active_user.set_solde(user1.get_solde());
  }
  if (active_user.get_id(3) == user2.get_id(3)) {
    active_user.set_solde(user2.get_solde());
  }
  active_user.log_in();
}

void setup()
{
  //Serial.begin(9600);
  init_reader();
  Wire.onReceive(receiveEvent);
  delay(DISPLAY_TIME);
  //load user's ID in objects
  for (int i = 0; i < ID_LENGTH; i++) {
    user1.set_id(DATABASE[0][i], i);
    user2.set_id(DATABASE[1][i], i);
  }
  user1.set_solde(1000);
  user2.set_solde(500);
  /*----------------Sensor-----------------------*/
  init_pins();
  sensor_capsule = false;
  sensor_capsule_1 = false;
  sensor_capsule_2 = false;
  sensor_capsule_3 = false;
  sensor_capsule_4 = false;
  /*----------------Led-----------------------*/
  FastLED.addLeds<WS2812, LED_PIN, GRB>(strip_leds, NUM_LEDS);
  /*----------------Servomoteur-----------------------*/
  //servo 1
  servo_1.pin = 8;
  servo_1.pos = POS_REST;
  order_servo_1.attach(servo_1.pin);
  order_servo_1.write(servo_1.pos);
  order_servo_1.detach();
  end_position = 0;
  //servo 2
  servo_2.pin = 9;
  servo_2.pos = POS_REST;
  order_servo_2.attach(servo_2.pin);
  order_servo_2.write(servo_2.pos);
  order_servo_2.detach();
  /*----------------LCD-----------------------*/
  LCD.begin(COLUMN_LCD, ROW_LCD);
  LCD.clear();
  /*----------------State Machine-----------------------*/
  leds_capsules(strip_leds, capsule_1, CRGB::Black);
  leds_capsules(strip_leds, capsule_2, CRGB::Black);
  leds_capsules(strip_leds, capsule_3, CRGB::Black);
  leds_capsules(strip_leds, capsule_4, CRGB::Black);
  state_machine = READ_RFID;
  /*----------------capsule-----------------------*/
  old_time = 0;
}
//-------------------------------------------------------------------------------------------
//----|Boucle Infinie|-----------------------------------------------------------------------
void loop()
{
  switch (state_machine)
  {
    case CHOICE_CAPSULE :
      display(state_machine, LCD);
      sensor_capsule_1 = READ_IND_SENS(IND_SENS_1);
      sensor_capsule_2 = READ_IND_SENS(IND_SENS_2);
      sensor_capsule_3 = READ_IND_SENS(IND_SENS_3);
      sensor_capsule_4 = READ_IND_SENS(IND_SENS_4);
      //switch on capsule colors upon availability
      sensor_capsule_1 ? leds_capsules(strip_leds, capsule_1, CRGB::Green) : leds_capsules(strip_leds, capsule_1, CRGB::Red);
      sensor_capsule_2 ? leds_capsules(strip_leds, capsule_2, CRGB::Green) : leds_capsules(strip_leds, capsule_2, CRGB::Red);
      sensor_capsule_3 ? leds_capsules(strip_leds, capsule_3, CRGB::Green) : leds_capsules(strip_leds, capsule_3, CRGB::Red);
      sensor_capsule_4 ? leds_capsules(strip_leds, capsule_4, CRGB::Green) : leds_capsules(strip_leds, capsule_4, CRGB::Red);

      choice_1_active = READ_TOUCH_SENS(TOUCH_SENS_1);
      choice_2_active = READ_TOUCH_SENS(TOUCH_SENS_2);
      choice_3_active = READ_TOUCH_SENS(TOUCH_SENS_3);
      choice_4_active = READ_TOUCH_SENS(TOUCH_SENS_4);
      cancel_active  =  READ_PUSH_BT(CANCEL_BUTTON);
      if (choice_1_active)
      {
        end_position = POS_CAPSULE_1;
      }
      else if (choice_2_active)
      {
        end_position = POS_CAPSULE_2;
      }
      else if (choice_3_active)
      {
        end_position = POS_CAPSULE_3;
      }
      else if (choice_4_active)
      {
        end_position = POS_CAPSULE_4;
      }
      if (choice_1_active || choice_2_active || choice_3_active || choice_4_active)
      {
        state_machine = CHECK_CAPSULE_AVAILABLE;
        LCD.clear();
      }
      else if (cancel_active || ((millis() - old_time) >= LOGOUT_TIME)) //checking 20s
      {
        LCD.clear();
        LCD.setCursor(LINE_ONE);
        LCD.print("Bienvenue");
        LCD.setCursor(LINE_TWO);
        LCD.print("Carte SVP");
        cancel_active = false;
        state_machine = TURN_OFF_LED;
      }
      else
      {
        state_machine = CHOICE_CAPSULE;
      }
      break;
    case CHECK_CAPSULE_AVAILABLE :
      if (choice_1_active)
      {
        num_sensor = IND_SENS_1;
      }
      else if (choice_2_active)
      {
        num_sensor = IND_SENS_2;
      }
      else if (choice_3_active)
      {
        num_sensor = IND_SENS_3;
      }
      else if (choice_4_active)
      {
        num_sensor = IND_SENS_4;
      }
      sensor_capsule = READ_IND_SENS(num_sensor);
      if (sensor_capsule)
      {
        state_machine = CHECK_MONEY_SUFFICIENT;
        old_time = millis();
        LCD.clear();
      }
      else
      {
        state_machine = CAPSULE_UNAVAILABLE;
      }
      break;
    case CAPSULE_UNAVAILABLE :
      display(state_machine, LCD);
      delay(DISPLAY_TIME);
      state_machine = CHOICE_CAPSULE;
      LCD.clear();
      break;
    case READ_RFID :
      display(state_machine, LCD);
      rfid = active_user.is_logged();
      if (rfid)
      {
        rfid = false;
        turn_on_light(strip_leds);
        old_time = millis();
        LCD.clear();
        state_machine = CHOICE_CAPSULE;
      }
      else
      {
        state_machine = READ_RFID;
      }
      break;
    case CHECK_MONEY_SUFFICIENT :
      argentSuffisant = active_user.get_solde();
      state_machine =  (argentSuffisant >= CAPSULE_PRICE) ? MONEY_SUFFICIENT : MONEY_INSUFFICIENT;
      break;
    case MONEY_SUFFICIENT :
      display(state_machine, LCD);
      state_machine = CONFIRMATION_PAYMENT;
      LCD.setCursor(LINE_TWO);
      LCD.print("Solde : ");
      //print floating number out of integer variable
      LCD.print((active_user.get_solde() / 100));
      LCD.print(".");
      LCD.print((active_user.get_solde() % 100));
      LCD.print(" CHF");
      delay(DISPLAY_TIME);
      old_time = millis();
      LCD.clear();
      break;
    case MONEY_INSUFFICIENT :
      display(state_machine, LCD);
      delay(DISPLAY_TIME);
      state_machine = CHOICE_CAPSULE;
      LCD.clear();
      break;
    case CONFIRMATION_PAYMENT :
      display(state_machine, LCD);
      confirm_active = READ_PUSH_BT(CONFIRM_BUTTON);
      cancel_active = READ_PUSH_BT(CANCEL_BUTTON);
      if (confirm_active)
      {
        state_machine = PAYMENT;
        confirm_active = false;
      }
      else if ((cancel_active) or ((millis() - old_time) >= LOGOUT_TIME))
      {
        cancel_active = false;
        state_machine = CHOICE_CAPSULE;
        LCD.clear();
      }
      else
      {
        state_machine = CONFIRMATION_PAYMENT;
      }
      break;
    case PAYMENT :
      display(state_machine, LCD);
      delay(DISPLAY_TIME);
      active_user.buy_capsule(CAPSULE_PRICE);
      //check active user and update solde (just for the demo)
      if (active_user.get_id(3) == user1.get_id(3)) {
        user1.set_solde(active_user.get_solde());
      }
      if (active_user.get_id(3) == user2.get_id(3)) {
        user2.set_solde(active_user.get_solde());
      }
      state_machine = DROPPING_CAPSULE;
      break;
    case DROPPING_CAPSULE :
      display(state_machine, LCD);
      if (choice_1_active or choice_2_active)
      {
        order_servo_1.attach(servo_1.pin);
        rotate_servo(servo_1, order_servo_1, end_position);
        servo_1.pos = end_position;
        order_servo_1.detach();
        if (choice_1_active)
        {
          end_position = POS_REST_1;
        }
        else
        {
          end_position = POS_REST;
        }
      }
      else if (choice_3_active or choice_4_active)
      {
        order_servo_2.attach(servo_2.pin);
        rotate_servo(servo_2, order_servo_2, end_position);
        servo_2.pos = end_position;
        order_servo_2.detach();
        if (choice_4_active)
        {
          end_position = POS_REST_2;
        }
        else
        {
          end_position = POS_REST;
        }
      }
      delay(DISPLAY_TIME);
      state_machine = CAPSULE_DROPPED;
      break;
    case CAPSULE_DROPPED :
      display(state_machine, LCD);
      if (choice_1_active or choice_2_active)
      {
        order_servo_1.attach(servo_1.pin);
        rotate_servo(servo_1, order_servo_1, end_position);
        order_servo_1.detach();
        delay(DISPLAY_TIME);
        servo_1.pos = end_position;
        choice_1_active = false;
        choice_2_active = false;
      }
      else if (choice_3_active or choice_4_active)
      {
        order_servo_2.attach(servo_2.pin);
        rotate_servo(servo_2, order_servo_2, end_position);
        order_servo_2.detach();
        servo_2.pos = end_position;
        choice_3_active = false;
        choice_4_active = false;
      }
      state_machine = TURN_OFF_LED;
      break;
    case  TURN_OFF_LED:
      turn_off_light(strip_leds);
      active_user.logout();
      leds_capsules(strip_leds, capsule_1, CRGB::Black);
      leds_capsules(strip_leds, capsule_2, CRGB::Black);
      leds_capsules(strip_leds, capsule_3, CRGB::Black);
      leds_capsules(strip_leds, capsule_4, CRGB::Black);
      state_machine = READ_RFID;
      delay(DISPLAY_TIME);
      LCD.clear();
      break;
    default :
      break;
  }
}

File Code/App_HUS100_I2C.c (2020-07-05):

//***
//Elatec Reader Source code -> used in AppBlaster.exe to create firmware image
//***
#include "twn4.sys.h"
#include "apptools.h"

#define MAXIDBYTES  10
#define MAXIDBITS   (MAXIDBYTES*8)

byte ID[MAXIDBYTES];
int IDBitCnt;
int TagType;

byte LastID[MAXIDBYTES];
int LastIDBitCnt;
int LastTagType;
const int I2CAddress = 0x30;

// If necessary adjust default parameters
#ifndef __APP_CONFIG_H__
    #define LFTAGTYPES        		0
    #define HFTAGTYPES        		0
#endif

const unsigned char AppManifest[] = { EXECUTE_APP, 1, EXECUTE_APP_ALWAYS, TLV_END };

// Setup tag types as configured in AppBlaster
void ConfigSetTagTypes(void)
{
	if (LFTAGTYPES || HFTAGTYPES)
    	SetTagTypes(LFTAGTYPES,HFTAGTYPES);
}

int main(void)
{
	//define communication mode I2C
	SetHostChannel(CHANNEL_I2C);
	I2CInit(I2CMODE_MASTER);
	// Set tag types
	ConfigSetTagTypes();
    // Make some noise at startup at low volume
    SetVolume(30);
    BeepLow();
    BeepHigh();
    // Continue with higher volume
    SetVolume(80);
    // No transponder found up to now
    LastTagType = NOTAG;
	while (true)
    {
        // Search a transponder
        if (SearchTag(&TagType,&IDBitCnt,ID,sizeof(ID)))
        {
			// Is this transponder new to us?
			if (TagType != LastTagType || IDBitCnt != LastIDBitCnt || !CompBits(ID,0,LastID,0,MAXIDBITS))
			{
				// Save this as known ID, before modifying the ID for proper output format
				CopyBits(LastID,0,ID,0,MAXIDBITS);
				LastIDBitCnt = IDBitCnt;
				LastTagType = TagType;
				//Sound a beep
				BeepHigh();
				I2CMasterStart();
				I2CMasterBeginWrite(I2CAddress);
				// Send UID
				for(int i = 0; i<=4;i++){ //Mifare/Legic ID length is 4 bytes
				I2CMasterTransmitByte(ID[i]);
				}
				I2CMasterStop();
			}
			StartTimer(2000);
        }
        if (TestTimer())
        {
            LastTagType = NOTAG;
        }
    }
}

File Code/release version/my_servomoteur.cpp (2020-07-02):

//--|Include user|---------------------------------------------------------------------------
#include "my_servomoteur.h"
//-------------------------------------------------------------------------------------------
void rotate_servo(sServo servo, Servo order_servo, uint16_t end_pos)
{
  if (end_pos > servo.pos)
  {
    for (servo.pos = servo.pos; servo.pos < end_pos; servo.pos++)
    {
      order_servo.write(servo.pos);
      delay(STEP_DELAY);
    }
  }
  else if (end_pos < servo.pos)
  {
    for (servo.pos = servo.pos; servo.pos > end_pos; servo.pos--)
    {
      order_servo.write(servo.pos);
      delay(STEP_DELAY);
    }
  }
}

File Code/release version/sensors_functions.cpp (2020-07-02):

#include "sensors_functions.h"
void init_pins() {
  // Inductive sensors pins as input
  pinMode(IND_SENS_1, INPUT);
  pinMode(IND_SENS_2, INPUT);
  pinMode(IND_SENS_3, INPUT);
  pinMode(IND_SENS_4, INPUT);
  // Touch sensors pins as input
  pinMode(TOUCH_SENS_1, INPUT);
  pinMode(TOUCH_SENS_2, INPUT);
  pinMode(TOUCH_SENS_3, INPUT);
  pinMode(TOUCH_SENS_4, INPUT);
  // Push buttons
  pinMode(CONFIRM_BUTTON, INPUT);
  pinMode(CANCEL_BUTTON, INPUT);
}

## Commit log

2020-06-22 Corrected driver path
2020-06-23 Added 3D parts
    [LCD_box_cover.SLDPRT, LCD_box_cover.STL, LCD_box_mounting.SLDPRT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]
2020-06-23 Added documentation
    [encoding_lug_reader.SLDPRT, encoding_lug_reader.STL]
2020-06-24 Added render
    [encoding_lug_reader.SLDPRT, encoding_lug_reader.STL]
2020-06-26 Added DXF files
    [00_00_Panneau_arriere.DXF, 00_00_Panneau_arriere.SLDDRW, 00_01_Panneau_arriere_droite.DXF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]
2020-06-27 Completed laser cut file
    [00_02_Panneau_arriere_gauche.DXF, 00_09_Panneau_haut_capsule.SLDDRW, 00_10_Panneau_machine_cafe.SLDDRW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]
2020-06-30 Modified disk part
    [02_00_Disque distribution.SLDDRW, 02_00_Disque_distribution.DXF, 02_00_Disque_distribution.SLDDRW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]
2020-07-02 edited led files
2020-07-05 Update nespresso_dispenser.ino
    J'ai modifier le nom de trois des états (CATCHING_CAPSULE -> DROPPING_CAPSULE, DROPPING_CAPSULE -> CAPSULE_DROPPED et COLOR_LED -> TURN_OFF_LEDS) car ils n'étaient plus cohérents avec la nouvelle mac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
2020-07-05 Update utility.h
    Même chose que pour le .ino j'ai modifier les noms de certains états pour être plus cohérents
